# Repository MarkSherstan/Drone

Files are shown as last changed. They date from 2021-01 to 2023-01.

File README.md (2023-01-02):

# Drone
Mechanical, electrical, and software package for a custom quadcopter drone.

## Mechanical 
Designed using Fusion 360 and 3D printed on a Prusa MK3 printer. 

## Electrical
Custom PCBs designed in KiCad for the brain, power distribution, and signal indication. 
- Flight Controller
- Power Distribution Board 
- Lights 

## Software
C++ and custom libraries for controlling and stabilizing the UAV. Compiled with PlatformIO.

## Future Ideas
### Electrical
- Design ESCs
- 3.3 V flight controller (8 MHz suffcient?)
- Polyfuses on outputs
- PDB also ESC (active cooling?) - Have regulated outputs 
- PDB is part of frame (1 Oz copper)
- More powerful chip - RPi / STM32 / 2560 - Internet connection?

### Software 
- Test the crystal: How much time are we loosing? Try different caps.

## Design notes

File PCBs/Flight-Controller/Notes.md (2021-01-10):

## Crystal Capacitor Calcs
CL= (CX1 * CX2)/(CX1 + CX2) + CSTRAY
CL = (CX * CX)/(CX + CX) + CSTRAY <= substitute CX for CX1 and CX2 since they equal each other
CL = (CX^2)/(2CX) + CSTRAY
CL = (CX/2) + CSTRAY
CL - CSTRAY = (CX/2)
2*(CL -CSTRAY) = CX

CX1 = CX2 = 2*(CL-CSTRAY)

CSTRAY approx 4pF

22/2 = 11 - 4 = 7 ish 

https://blog.adafruit.com/2012/01/24/choosing-the-right-crystal-and-caps-for-your-design/
C1, C2 = 2*CL – 2*Cstray

https://forum.digikey.com/t/crystal-oscillator-load-cap-selection/1915
C1, C2 = 2*(CL) - Cstray

load capacitance of crystal * 2 - stray cap pin and trace = cap size 
https://www.microchip.com/forums/m881105.aspx
https://www.sparkfun.com/products/94

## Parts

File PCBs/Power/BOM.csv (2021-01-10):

Reference(s) | Qty | Value | LibPart | Footprint | Digi-Key # | Manufacturer | Manufacturer #
H1, H2, H3, H4 | 4 | M2 | Mechanical:MountingHole | MountingHole:MountingHole_2.2mm_M2_ISO14580_Pad
J1 | 1 | Power in SMD | Connector_Generic:Conn_01x02 | Custom:SMD-Power
J2 | 1 | Power in THR | Connector_Generic:Conn_01x02 | Custom:THR-Power
J3 | 1 | Corner 1 | Connector_Generic:Conn_01x02 | Custom:Corner-Pad
J4 | 1 | Corner 2 | Connector_Generic:Conn_01x02 | Custom:Corner-Pad
J5 | 1 | Corner 3 | Connector_Generic:Conn_01x02 | Custom:Corner-Pad
J6 | 1 | Corner 4 | Connector_Generic:Conn_01x02 | Custom:Corner-Pad
J7 | 1 | Flight Controller | Connector_Generic:Conn_01x06 | Connector_JST:JST_GH_BM06B-GHS-TBT_1x06-1MP_P1.25mm_Vertical | 455-1582-1-ND | JST Sales America Inc. | BM06B-GHS-TBT(LF)(SN)(N)
J8 | 1 | Flight Controller | Connector_Generic:Conn_01x06 | Connector_JST:JST_GH_SM06B-GHS-TB_1x06-1MP_P1.25mm_Horizontal | 455-1568-1-ND | JST Sales America Inc. | SM06B-GHS-TB(LF)(SN)

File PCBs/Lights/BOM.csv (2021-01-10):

Reference(s) | Qty | Value | LibPart | Footprint | Digi-Key # | Digi-Key Link Digi Link Digi-Key Link | Manufacturer | Manufacturer #
C1 | 1 | 1 uF 16V 10% | Device:C | Capacitor_SMD:C_0603_1608Metric_Pad1.05x0.95mm_HandSolder
D1 | 1 | See Notes | Device:LED | LED_SMD:LED_0603_1608Metric_Pad1.05x0.95mm_HandSolder
H1, H2 | 2 | M2 | Mechanical:MountingHole | MountingHole:MountingHole_2.2mm_M2_ISO14580_Pad
J1 | 1 | Conn_01x02 | Connector_Generic:Conn_01x02 | Connector_JST:JST_GH_SM02B-GHS-TB_1x02-1MP_P1.25mm_Horizontal | 455-1564-1-ND | https://www.digikey.ca/en/products/detail/jst-sales-america-inc/SM02B-GHS-TB-LF-SN/807786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 | JST Sales America Inc. | SM02B-GHS-TB(LF)(SN)
R1 | 1 | See Notes | Device:R | Resistor_SMD:R_0603_1608Metric_Pad1.05x0.95mm_HandSolder

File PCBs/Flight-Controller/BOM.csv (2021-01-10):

Reference(s) | Qty | Value | LibPart | Footprint | Digi-Key # | Manufacturer | Manufacturer # | Digi-Key Link
C1, C10, C11, C12, C18, C22 | 6 | 1uF 16V X7R 10% | Device:C | Capacitor_SMD:C_0603_1608Metric_Pad1.05x0.95mm_HandSolder
C2, C6, C9, C13, C14, C15, C21, C23 | 8 | 0.1uF 16V X7R 10% | Device:C | Capacitor_SMD:C_0603_1608Metric_Pad1.05x0.95mm_HandSolder
C3 | 1 | 10nF 16V X7R 10% | Device:C | Capacitor_SMD:C_0603_1608Metric_Pad1.05x0.95mm_HandSolder
C4 | 1 | 0.47uF 16V X7R 10% | Device:C | Capacitor_SMD:C_0603_1608Metric_Pad1.05x0.95mm_HandSolder
C5 | 1 | 2.2uF 16V X7R 10% | Device:C | Capacitor_SMD:C_0603_1608Metric_Pad1.05x0.95mm_HandSolder
C7, C8 | 2 | 22pF 12V X7R 2% | Device:C | Capacitor_SMD:C_0603_1608Metric_Pad1.05x0.95mm_HandSolder
C16 | 1 | 0.1uF 20V X7R 10% | Device:C | Capacitor_SMD:C_0603_1608Metric_Pad1.05x0.95mm_HandSolder
C17 | 1 | 10uF 20V 20% | Device:CP | Capacitor_SMD:C_0603_1608Metric_Pad1.05x0.95mm_HandSolder
C19, C20 | 2 | 22uF 16V 20% | Device:CP | Capacitor_SMD:C_0603_1608Metric_Pad1.05x0.95mm_HandSolder
D1 | 1 | LED_RGB | Custom:LED_RGB | Custom:RGB_LED | 1080-EAST1616RGBA4CT-ND | Everlight Electronics Co Ltd | EAST1616RGBA4 | https://www.digikey.ca/en/products/detail/everlight-electronics-co-ltd/EAST1616RGBA4/11200796
D2, D3 | 2 | Green 2.2V 20mA | Device:LED | LED_SMD:LED_0603_1608Metric_Pad1.05x0.95mm_HandSolder
D4 | 1 | 75V 150mA | Device:D | Diode_SMD:D_0603_1608Metric_Pad1.05x0.95mm_HandSolder | TS4148CRZGCT-ND | Taiwan Semiconductor Corporation | TS4148C RZG | https://www.digikey.ca/en/products/detail/taiwan-semiconductor-corporation/TS4148C-RZG/7359811
D5, D6 | 2 | Orange 2V 20mA | Device:LED | LED_SMD:LED_0603_1608Metric_Pad1.05x0.95mm_HandSolder
F1 | 1 | PTC 15V 500mA | Device:Polyfuse_Small | Fuse:Fuse_1206_3216Metric_Pad1.42x1.75mm_HandSolder | 283-3140-1-ND | Eaton - Electronics Division | PTS120615V050 | https://www.digikey.ca/en/products/detail/eaton-electronics-division/PTS120615V050/2639137
FB1 | 1 | Ferrite 30 ohm 1 line | Device:Ferrite_Bead | Resistor_SMD:R_0603_1608Metric_Pad1.05x0.95mm_HandSolder | MH1608-300YCT-ND | Bourns Inc. | MH1608-300Y | https://www.digikey.ca/en/products/detail/bourns-inc/MH1608-300Y/1970497
H1, H2, H3, H4 | 4 | M2 | Mechanical:MountingHole | MountingHole:MountingHole_2.2mm_M2_ISO7380_Pad
J1 | 1 | ESC_1 | Connector_Generic:Conn_01x05 | Connector_JST:JST_GH_BM05B-GHS-TBT_1x05-1MP_P1.25mm_Vertical | 455-1581-1-ND | JST Sales America Inc. | BM05B-GHS-TBT(LF)(SN)(N) | https://www.digikey.ca/en/products/detail/jst-sales-america-inc/BM05B-GHS-TBT-LF-SN-N/807803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
J2 | 1 | Receiver | Connector_Generic:Conn_01x07 | Connector_JST:JST_GH_BM07B-GHS-TBT_1x07-1MP_P1.25mm_Vertical | 455-1583-1-ND | JST Sales America Inc. | BM07B-GHS-TBT(LF)(SN)(N) | https://www.digikey.ca/en/products/detail/jst-sales-america-inc/BM07B-GHS-TBT-LF-SN-N/807805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
J3 | 1 | ESC_2 | Connector_Generic:Conn_01x05 | Connector_JST:JST_GH_BM05B-GHS-TBT_1x05-1MP_P1.25mm_Vertical | 455-1581-1-ND | JST Sales America Inc. | BM05B-GHS-TBT(LF)(SN)(N) | https://www.digikey.ca/en/products/detail/jst-sales-america-inc/BM05B-GHS-TBT-LF-SN-N/807803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
J4 | 1 | ICSP | Connector_Generic:Conn_02x03_Odd_Even | Connector_PinHeader_2.54mm:PinHeader_2x03_P2.54mm_Vertical
J5 | 1 | ESC_3 | Connector_Generic:Conn_01x05 | Connector_JST:JST_GH_BM05B-GHS-TBT_1x05-1MP_P1.25mm_Vertical | 455-1581-1-ND | JST Sales America Inc. | BM05B-GHS-TBT(LF)(SN)(N) | https://www.digikey.ca/en/products/detail/jst-sales-america-inc/BM05B-GHS-TBT-LF-SN-N/807803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
J6 | 1 | Aux | Connector_Generic:Conn_01x04 | Connector_JST:JST_GH_BM04B-GHS-TBT_1x04-1MP_P1.25mm_Vertical | 455-1580-1-ND | JST Sales America Inc. | BM04B-GHS-TBT(LF)(SN)(N) | https://www.digikey.ca/en/products/detail/jst-sales-america-inc/BM04B-GHS-TBT-LF-SN-N/807802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
J7 | 1 | ESC_4 | Connector_Generic:Conn_01x05 | Connector_JST:JST_GH_BM05B-GHS-TBT_1x05-1MP_P1.25mm_Vertical | 455-1581-1-ND | JST Sales America Inc. | BM05B-GHS-TBT(LF)(SN)(N) | https://www.digikey.ca/en/products/detail/jst-sales-america-inc/BM05B-GHS-TBT-LF-SN-N/807803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
J8 | 1 | Power_In | Connector_Generic:Conn_01x06 | Connector_JST:JST_GH_BM06B-GHS-TBT_1x06-1MP_P1.25mm_Vertical | 455-1582-1-ND | JST Sales America Inc. | BM06B-GHS-TBT(LF)(SN)(N) | https://www.digikey.ca/en/products/detail/jst-sales-america-inc/BM06B-GHS-TBT-LF-SN-N/807804
J9 | 1 | USB_B_Micro | Connector:USB_B_Micro | Connector_USB:USB_Micro-B_Molex-105017-0001 | WM1399CT-ND | Molex | 105017-0001 | https://www.digikey.ca/en/products/detail/molex/1050170001/2350832
Q1, Q2 | 2 | BSS138 | Transistor_FET:BSS138 | Package_TO_SOT_SMD:SOT-23 | BSS138CT-ND | ON Semiconductor | BSS138 | https://www.digikey.ca/en/products/detail/on-semiconductor/BSS138/244210
Q3, Q4 | 2 | PMV48XP,215 | Device:Q_PMOS_GSD | Package_TO_SOT_SMD:SOT-23 | 1727-5907-1-ND | Nexperia USA Inc. | PMV48XP,215 | https://www.digikey.ca/en/products/detail/nexperia-usa-inc/PMV48XP215/2744664
R1 | 1 | 3.2 kohm 1% | Device:R | Resistor_SMD:R_0603_1608Metric_Pad1.05x0.95mm_HandSolder
R2 | 1 | 2 kohm 1% | Device:R | Resistor_SMD:R_0603_1608Metric_Pad1.05x0.95mm_HandSolder
R3, R5 | 2 | 100 ohm 5% | Device:R | Resistor_SMD:R_0603_1608Metric_Pad1.05x0.95mm_HandSolder
R4, R6 | 2 | 150 ohm 5% | Device:R | Resistor_SMD:R_0603_1608Metric_Pad1.05x0.95mm_HandSolder
R7 | 1 | 55 ohm 5% | Device:R | Resistor_SMD:R_0603_1608Metric_Pad1.05x0.95mm_HandSolder
R8, R9, R10, R11, R12, R13, R14, R17, R18, R19 | 10 | 10 kohm 5% | Device:R | Resistor_SMD:R_0603_1608Metric_Pad1.05x0.95mm_HandSolder
R15, R16 | 2 | 1 kohm 5% | Device:R | Resistor_SMD:R_0603_1608Metric_Pad1.05x0.95mm_HandSolder
R20, R21 | 2 | 22 ohm 1% | Device:R | Resistor_SMD:R_0603_1608Metric_Pad1.05x0.95mm_HandSolder
RV1, RV2 | 2 | 5V 0.5pF | Device:Varistor | Resistor_SMD:R_0603_1608Metric_Pad1.05x0.95mm_HandSolder | CG0603MLC-05ECT-ND | Bourns Inc. | CG0603MLC-05E | https://www.digikey.ca/en/products/detail/bourns-inc/CG0603MLC-05E/2538084
SW1 | 1 | Push-Switch | Custom:Push-Switch | Custom:Switch | CKN10361CT-ND | C&K | RS-187R05A2-DS MT RT | https://www.digikey.ca/en/products/detail/c-k/RS-187R05A2-DS-MT-RT/2747186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
U1 | 1 | MCP6001U | Amplifier_Operational:MCP6001U | Package_TO_SOT_SMD:SOT-23-5 | MCP6001UT-I/OTCT-ND | Microchip Technology | MCP6001UT-I/OT | https://www.digikey.ca/en/products/detail/microchip-technology/MCP6001UT-I-OT/562450
U2 | 1 | ICM-20689 | Custom:ICM-20689 | Package_DFN_QFN:QFN-24-1EP_4x4mm_P0.5mm_EP2.8x2.8mm | 1428-1059-1-ND | TDK InvenSense | ICM-20689 | https://www.digikey.ca/en/products/detail/tdk-invensense/ICM-20689/5872869
U3 | 1 | ATmega32U4-AU | Flight-Controller-PCB-rescue:ATmega32U4-AU-MCU_Microchip_ATmega-Flight-Controller-PCB-rescue | Package_QFP:TQFP-44_10x10mm_P0.8mm | ATMEGA32U4RC-AU-ND | Microchip Technology | ATMEGA32U4RC-AU | https://www.digikey.ca/en/products/detail/microchip-technology/ATMEGA32U4RC-AU/2507982
U4 | 1 | LM1117-5.0 | Custom:LM1117-5.0 | Package_TO_SOT_SMD:SOT-223 | LM1117IMP-5.0/NOPBCT-ND | Texas Instruments | LM1117IMP-5.0/NOPB | https://www.digikey.ca/en/products/detail/texas-instruments/LM1117IMP-5-0-NOPB/482940
U5 | 1 | LP2985-3.3 | Regulator_Linear:LP2985-3.3 | Package_TO_SOT_SMD:SOT-23-5 | 296-18476-1-ND | Texas Instruments | LP2985-33DBVR | https://www.digikey.ca/en/products/detail/texas-instruments/LP2985-33DBVR/809759
Y1 | 1 | 16MHz, CL 7pF | Device:Crystal | Custom:Crystal | 535-14027-1-ND | Abracon LLC | ABM8W-16.0000MHZ-7-D1X-T3 | https://www.digikey.ca/en/products/detail/abracon-llc/ABM8W-16-0000MHZ-7-D1X-T3/7172798

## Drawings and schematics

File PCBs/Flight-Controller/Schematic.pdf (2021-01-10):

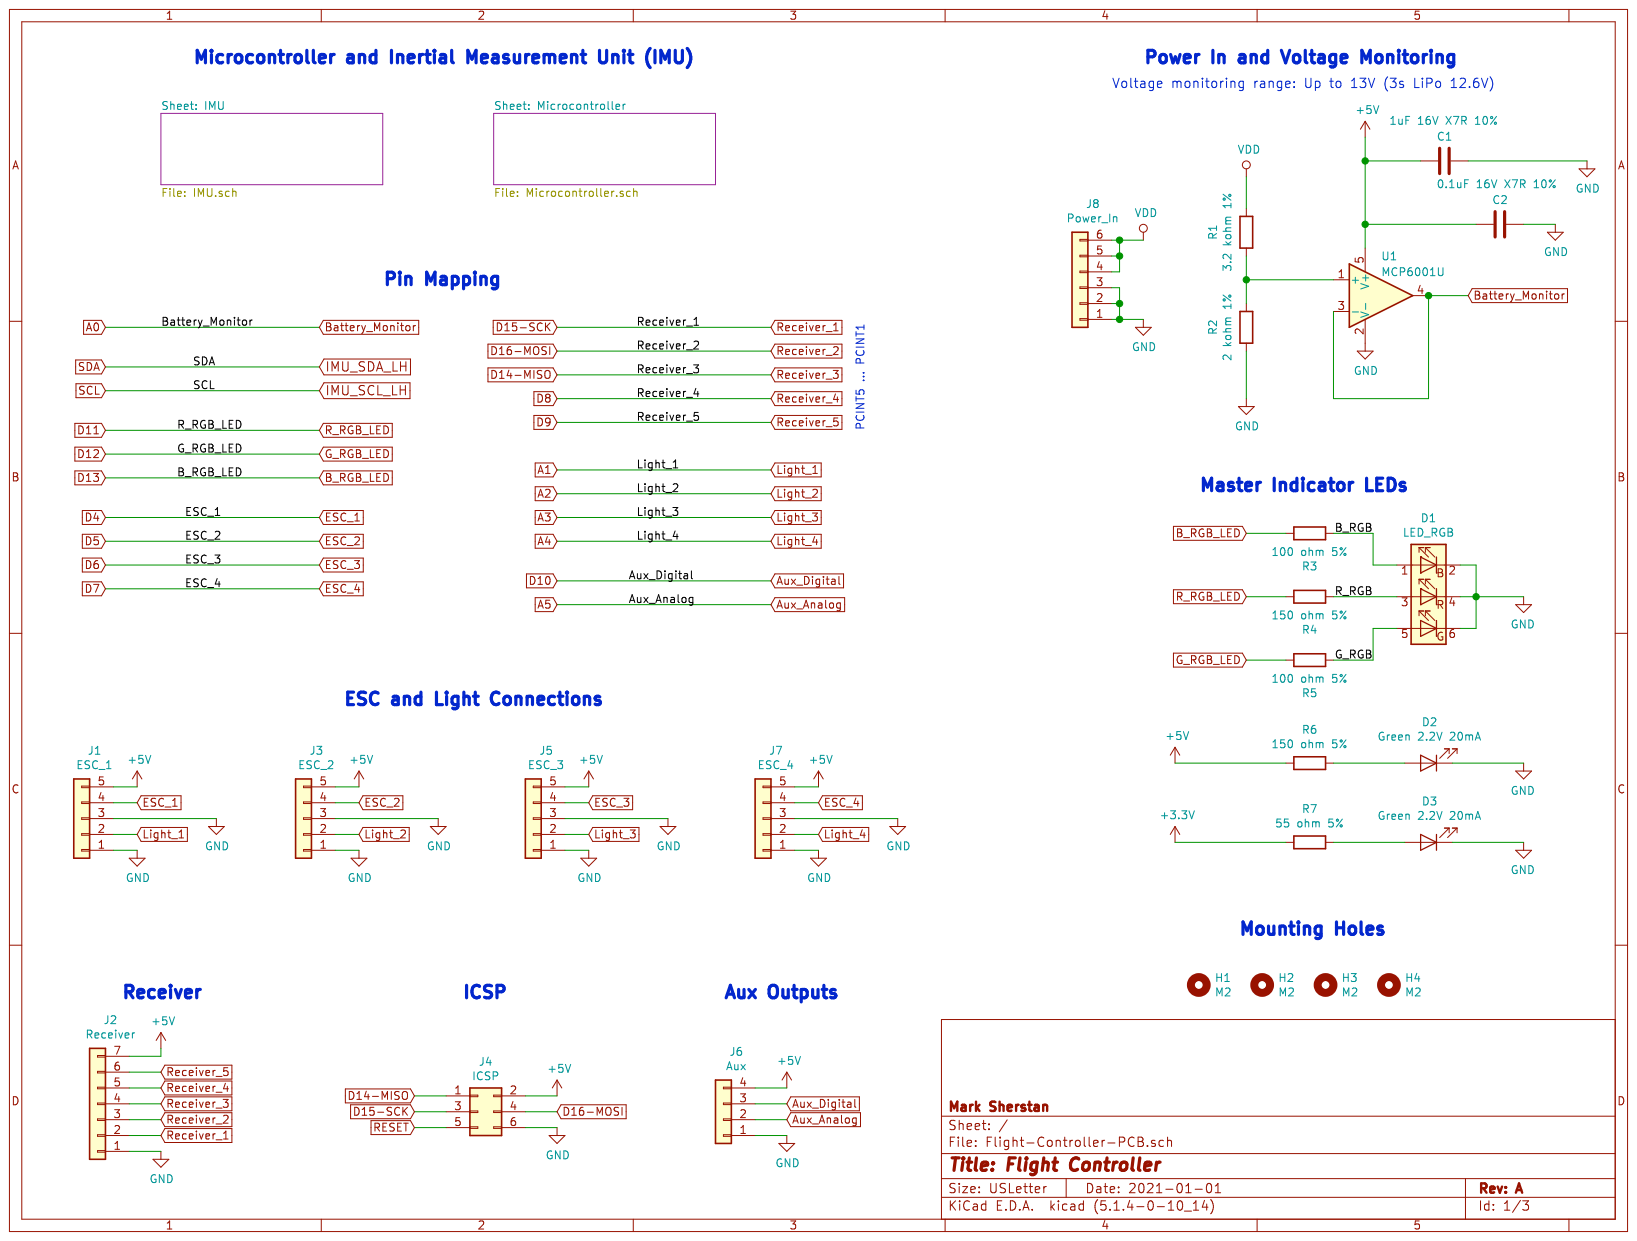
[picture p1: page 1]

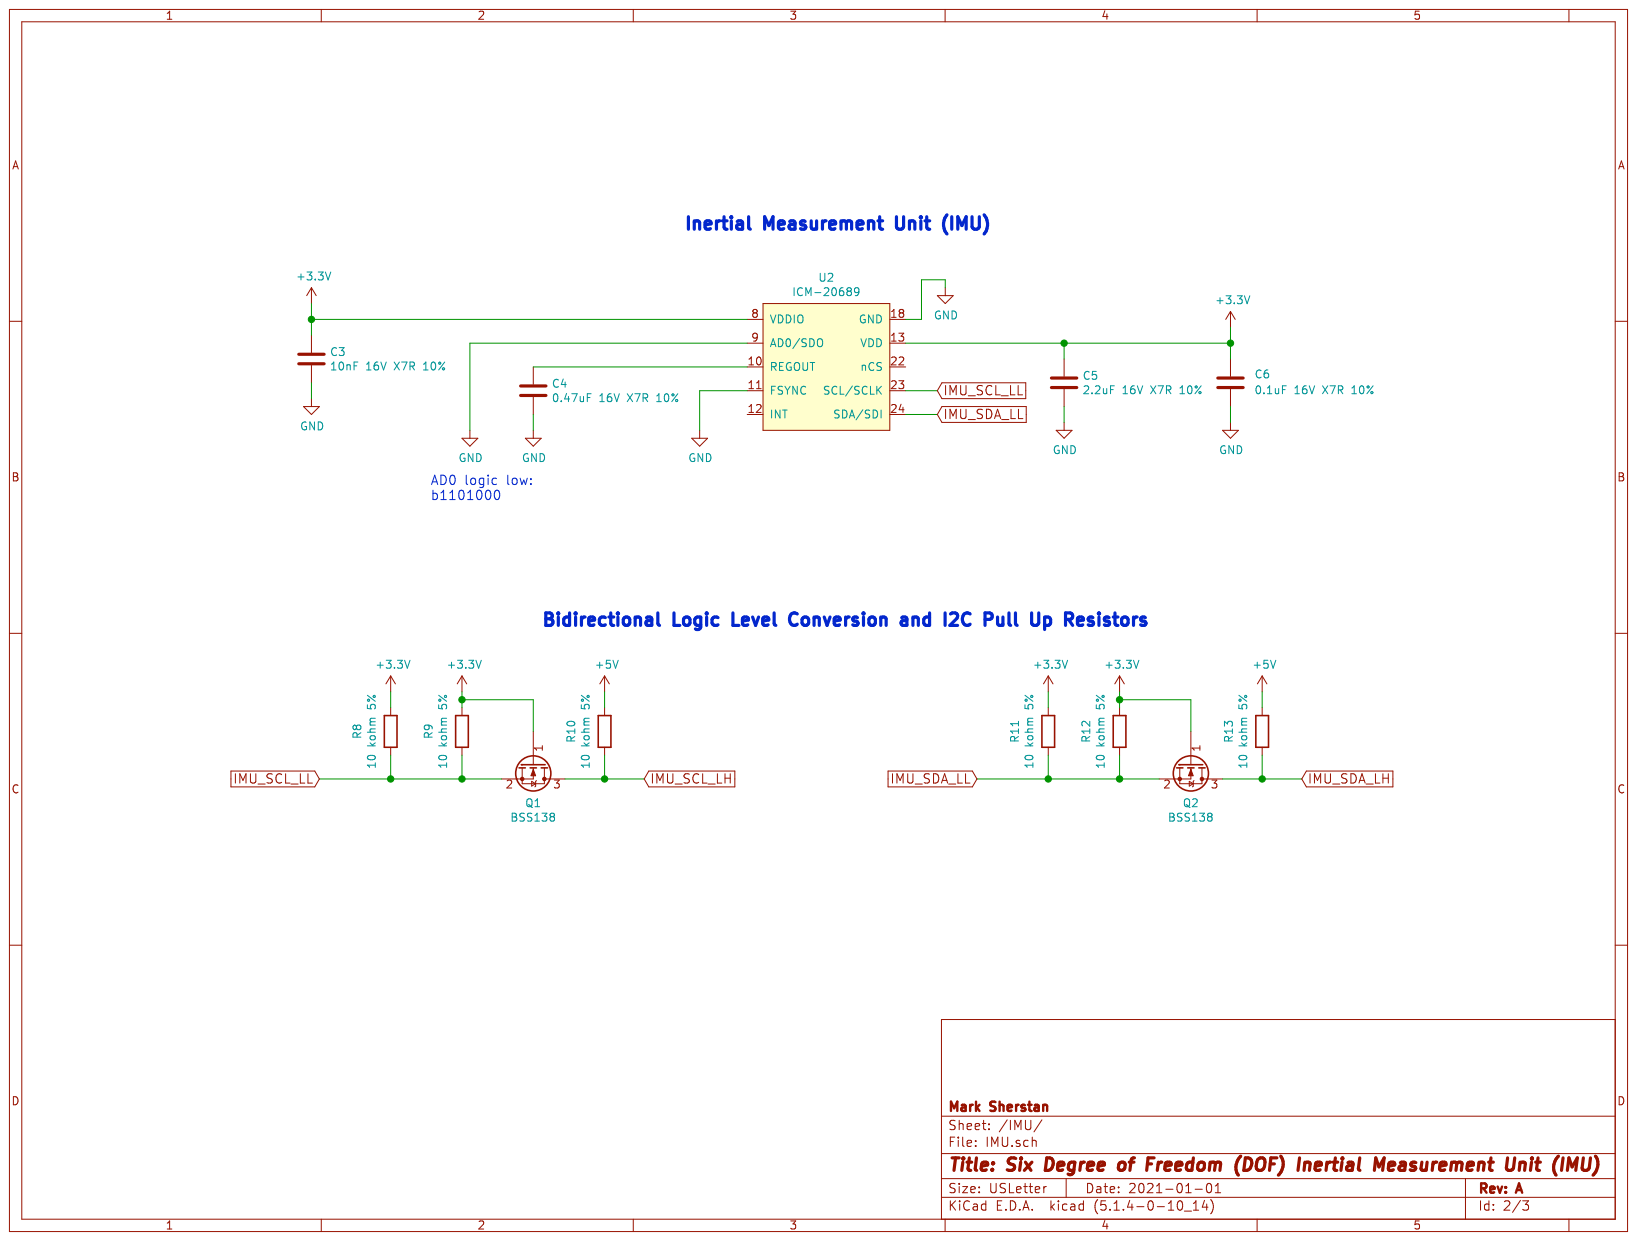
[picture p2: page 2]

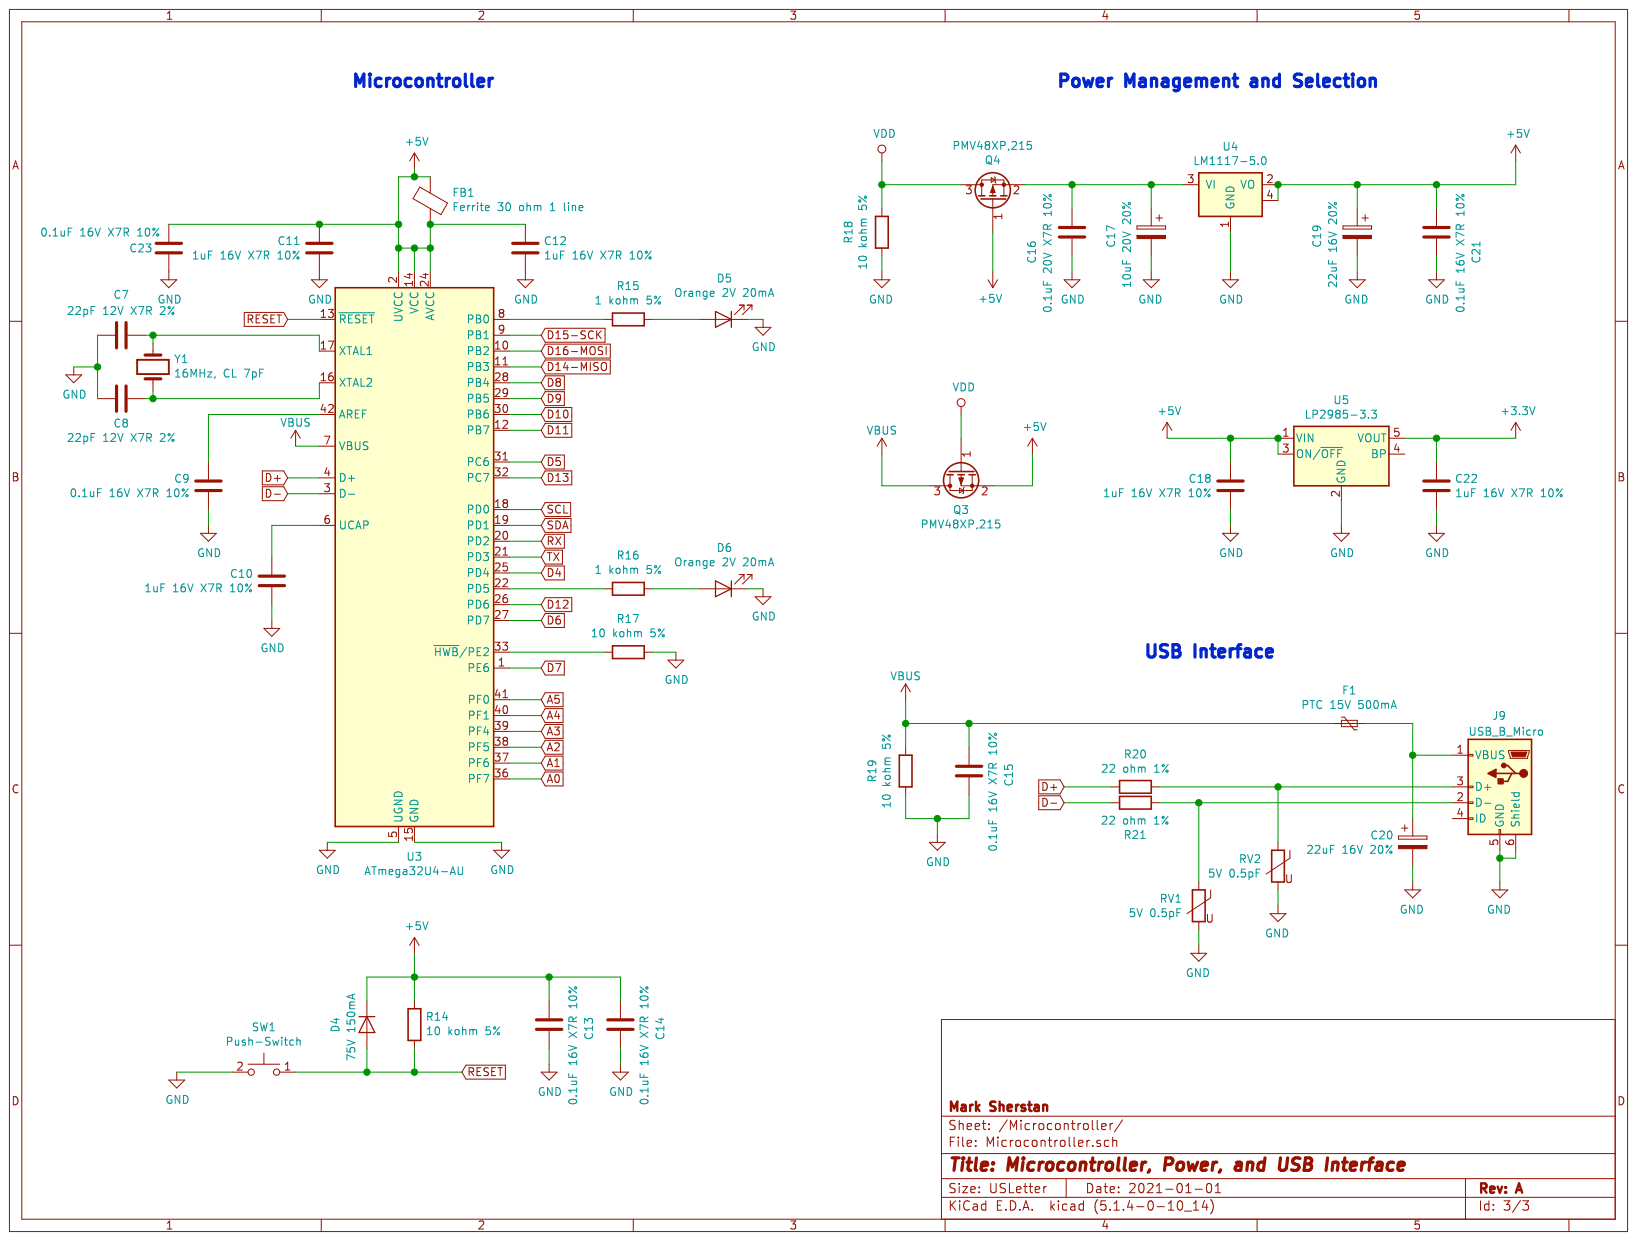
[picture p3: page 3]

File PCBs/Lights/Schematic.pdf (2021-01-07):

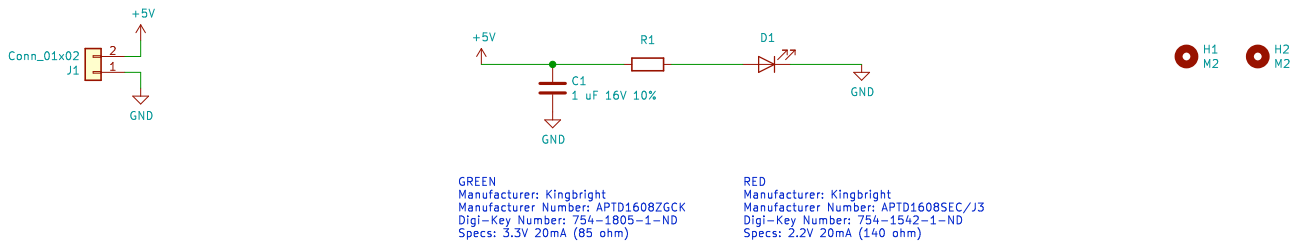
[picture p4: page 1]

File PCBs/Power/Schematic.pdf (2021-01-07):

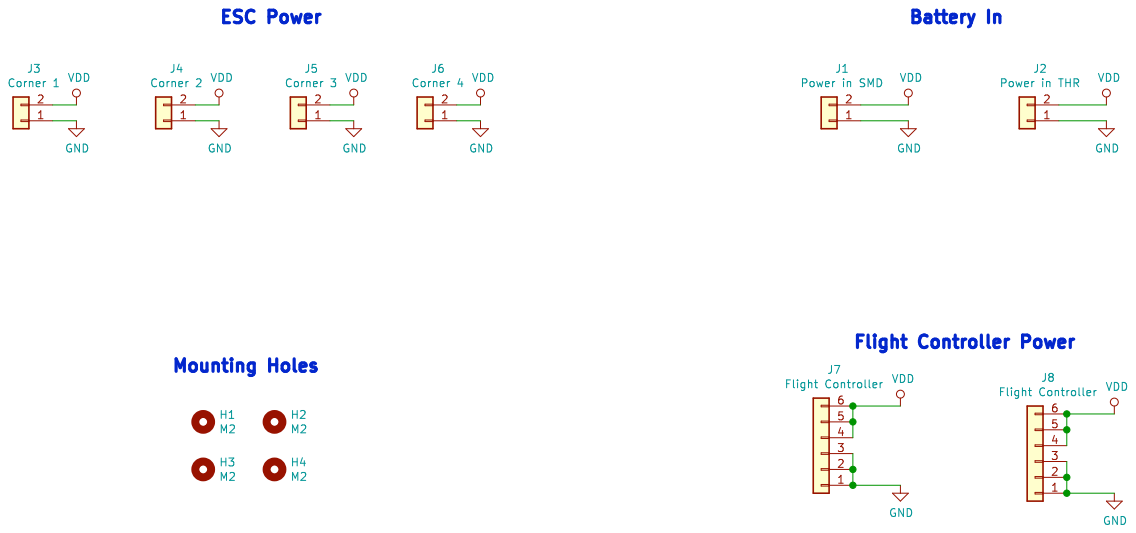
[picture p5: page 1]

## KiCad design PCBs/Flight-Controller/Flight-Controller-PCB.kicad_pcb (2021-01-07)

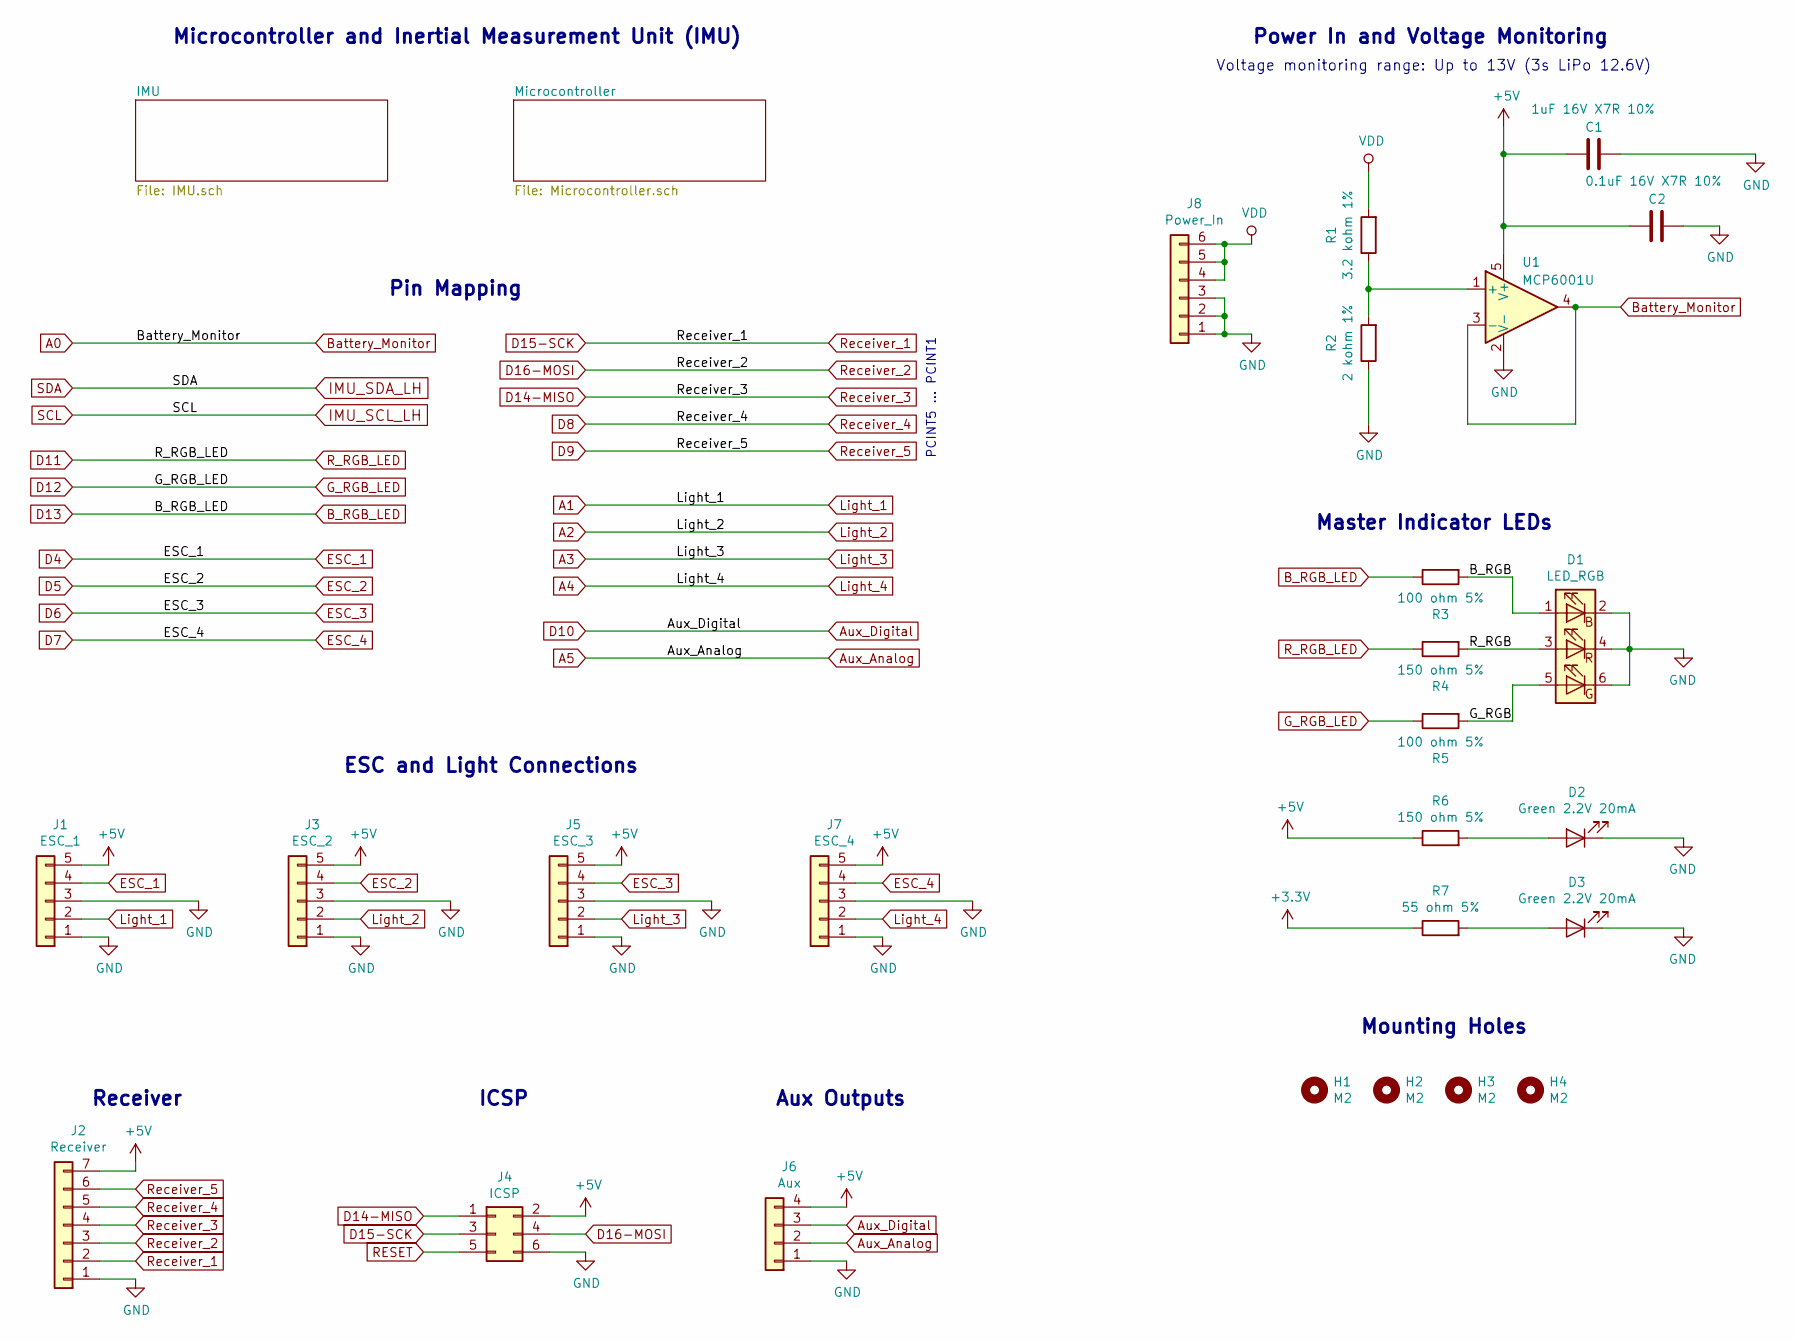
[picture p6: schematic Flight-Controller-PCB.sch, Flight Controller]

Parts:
C1: 1uF 16V X7R 10%; C_0603_1608Metric_Pad1.05x0.95mm_HandSolder
C2: 0.1uF 16V X7R 10%; C_0603_1608Metric_Pad1.05x0.95mm_HandSolder
D1: LED_RGB; RGB_LED; Manufacturer # EAST1616RGBA4; Digi-Key # 1080-EAST1616RGBA4CT-ND
D2, D3: Green 2.2V 20mA; LED_0603_1608Metric_Pad1.05x0.95mm_HandSolder
H1, H2, H3, H4: M2; MountingHole_2.2mm_M2_ISO7380_Pad
J1: ESC_1; JST_GH_BM05B-GHS-TBT_1x05-1MP_P1.25mm_Vertical; Manufacturer # BM05B-GHS-TBT(LF)(SN)(N); Digi-Key # 455-1581-1-ND
J2: Receiver; JST_GH_BM07B-GHS-TBT_1x07-1MP_P1.25mm_Vertical; Manufacturer # BM07B-GHS-TBT(LF)(SN)(N); Digi-Key # 455-1583-1-ND
J3: ESC_2; JST_GH_BM05B-GHS-TBT_1x05-1MP_P1.25mm_Vertical; Manufacturer # BM05B-GHS-TBT(LF)(SN)(N); Digi-Key # 455-1581-1-ND
J4: ICSP; PinHeader_2x03_P2.54mm_Vertical
J5: ESC_3; JST_GH_BM05B-GHS-TBT_1x05-1MP_P1.25mm_Vertical; Manufacturer # BM05B-GHS-TBT(LF)(SN)(N); Digi-Key # 455-1581-1-ND
J6: Aux; JST_GH_BM04B-GHS-TBT_1x04-1MP_P1.25mm_Vertical; Manufacturer # BM04B-GHS-TBT(LF)(SN)(N); Digi-Key # 455-1580-1-ND
J7: ESC_4; JST_GH_BM05B-GHS-TBT_1x05-1MP_P1.25mm_Vertical; Manufacturer # BM05B-GHS-TBT(LF)(SN)(N); Digi-Key # 455-1581-1-ND
J8: Power_In; JST_GH_BM06B-GHS-TBT_1x06-1MP_P1.25mm_Vertical; Manufacturer # BM06B-GHS-TBT(LF)(SN)(N); Digi-Key # 455-1582-1-ND
R1: 3.2 kohm 1%; R_0603_1608Metric_Pad1.05x0.95mm_HandSolder
R2: 2 kohm 1%; R_0603_1608Metric_Pad1.05x0.95mm_HandSolder
R3, R5: 100 ohm 5%; R_0603_1608Metric_Pad1.05x0.95mm_HandSolder
R4, R6: 150 ohm 5%; R_0603_1608Metric_Pad1.05x0.95mm_HandSolder
R7: 55 ohm 5%; R_0603_1608Metric_Pad1.05x0.95mm_HandSolder
U1: MCP6001U; SOT-23-5; Manufacturer # MCP6001UT-I/OT; Digi-Key # MCP6001UT-I/OTCT-ND

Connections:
+3V3: R7.1; also elsewhere on the board
+5V: C1.2, C2.2, J1.5, J2.7, J3.5, J4.2, J5.5, J6.4, J7.5, R6.1, U1.5 (V+); also elsewhere on the board
/B_RGB: D1.1 (RA), R3.2
/G_RGB: D1.5 (BA), R5.2
/R_RGB: D1.3 (GA), R4.2
A0: U1.3 (-), U1.4; also elsewhere on the board
A1: J1.2; also elsewhere on the board
A2: J3.2; also elsewhere on the board
A3: J5.2; also elsewhere on the board
A4: J7.2; also elsewhere on the board
A5: J6.2; also elsewhere on the board
Aux_Digital: J6.3; also elsewhere on the board
B_RGB_LED: R3.1; also elsewhere on the board
D4: J1.4; also elsewhere on the board
D5: J3.4; also elsewhere on the board
D6: J5.4; also elsewhere on the board
D7: J7.4; also elsewhere on the board
D8: J2.5; also elsewhere on the board
D9: J2.6; also elsewhere on the board
D11: R4.1; also elsewhere on the board
D12: R5.1; also elsewhere on the board
D14-MISO: J2.4, J4.1; also elsewhere on the board
D15-SCK: J2.2, J4.3; also elsewhere on the board
D16-MOSI: J2.3, J4.4; also elsewhere on the board
GND: C1.1, C2.1, D1.2 (RK), D1.4 (GK), D1.6 (BK), D2.1 (K), D3.1 (K), J1.1, J1.3, J2.1, J3.1, J3.3, J4.6, J5.1, J5.3, J6.1, J7.1, J7.3, J8.1, J8.2, J8.3, R2.1, U1.2 (V-); also elsewhere on the board
unnamed: D2.2 (A), R6.2
unnamed: D3.2 (A), R7.2
unnamed: R1.1, R2.2, U1.1 (+)
RESET: J4.5; also elsewhere on the board
VDD: J8.4, J8.5, J8.6, R1.2; also elsewhere on the board

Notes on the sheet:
Power In and Voltage Monitoring
Microcontroller and Inertial Measurement Unit (IMU)
Pin Mapping
ESC and Light Connections
Mounting Holes
Voltage monitoring range: Up to 13V (3s LiPo 12.6V)
Receiver
Aux Outputs
Master Indicator LEDs
ICSP
PCINT5 … PCINT1

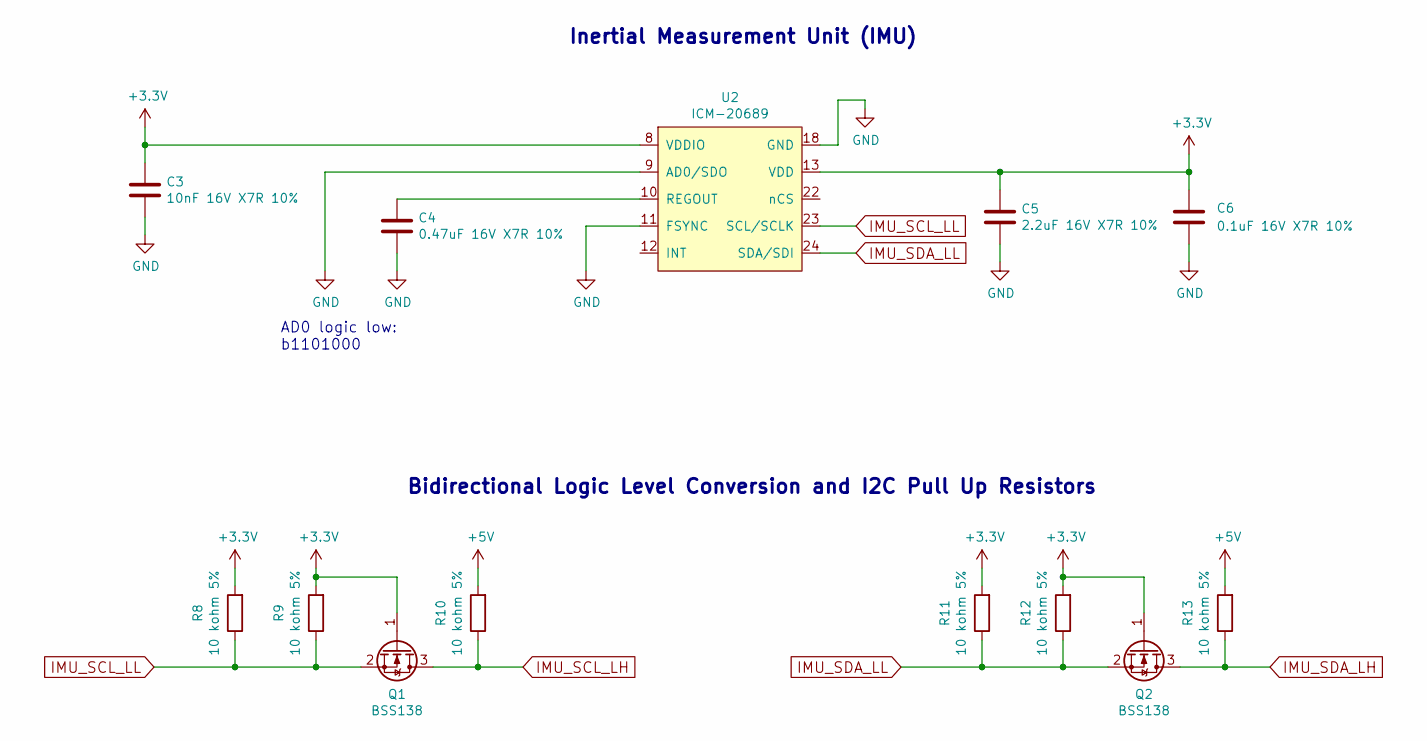
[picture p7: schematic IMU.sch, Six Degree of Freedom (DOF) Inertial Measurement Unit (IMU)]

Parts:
C3: 10nF 16V X7R 10%; C_0603_1608Metric_Pad1.05x0.95mm_HandSolder
C4: 0.47uF 16V X7R 10%; C_0603_1608Metric_Pad1.05x0.95mm_HandSolder
C5: 2.2uF 16V X7R 10%; C_0603_1608Metric_Pad1.05x0.95mm_HandSolder
C6: 0.1uF 16V X7R 10%; C_0603_1608Metric_Pad1.05x0.95mm_HandSolder
Q1, Q2: BSS138; SOT-23; Manufacturer # BSS138; Digi-Key # BSS138CT-ND
R8, R9, R10, R11, R12, R13: 10 kohm 5%; R_0603_1608Metric_Pad1.05x0.95mm_HandSolder
U2: ICM-20689; QFN-24-1EP_4x4mm_P0.5mm_EP2.8x2.8mm; Manufacturer # ICM-20689; Digi-Key # 1428-1059-1-ND

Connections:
+3V3: C3.1, C5.1, C6.2, Q1.1 (G), Q2.1 (G), R8.2, R9.2, R11.2, R12.2, U2.8 (VDDIO), U2.13 (VDD); also elsewhere on the board
+5V: R10.2, R13.2; also elsewhere on the board
GND: C3.2, C4.2, C5.2, C6.1, U2.9 (AD0/SDO), U2.11 (FSYNC), U2.18 (GND); also elsewhere on the board
IMU_SCL_LL: Q1.2 (S), R8.1, R9.1, U2.23 (SCL/SCLK)
IMU_SDA_LL: Q2.2 (S), R11.1, R12.1, U2.24 (SDA/SDI)
unnamed: C4.1, U2.10 (REGOUT)

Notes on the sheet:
AD0 logic low: b1101000
Inertial Measurement Unit (IMU)
Bidirectional Logic Level Conversion and I2C Pull Up Resistors

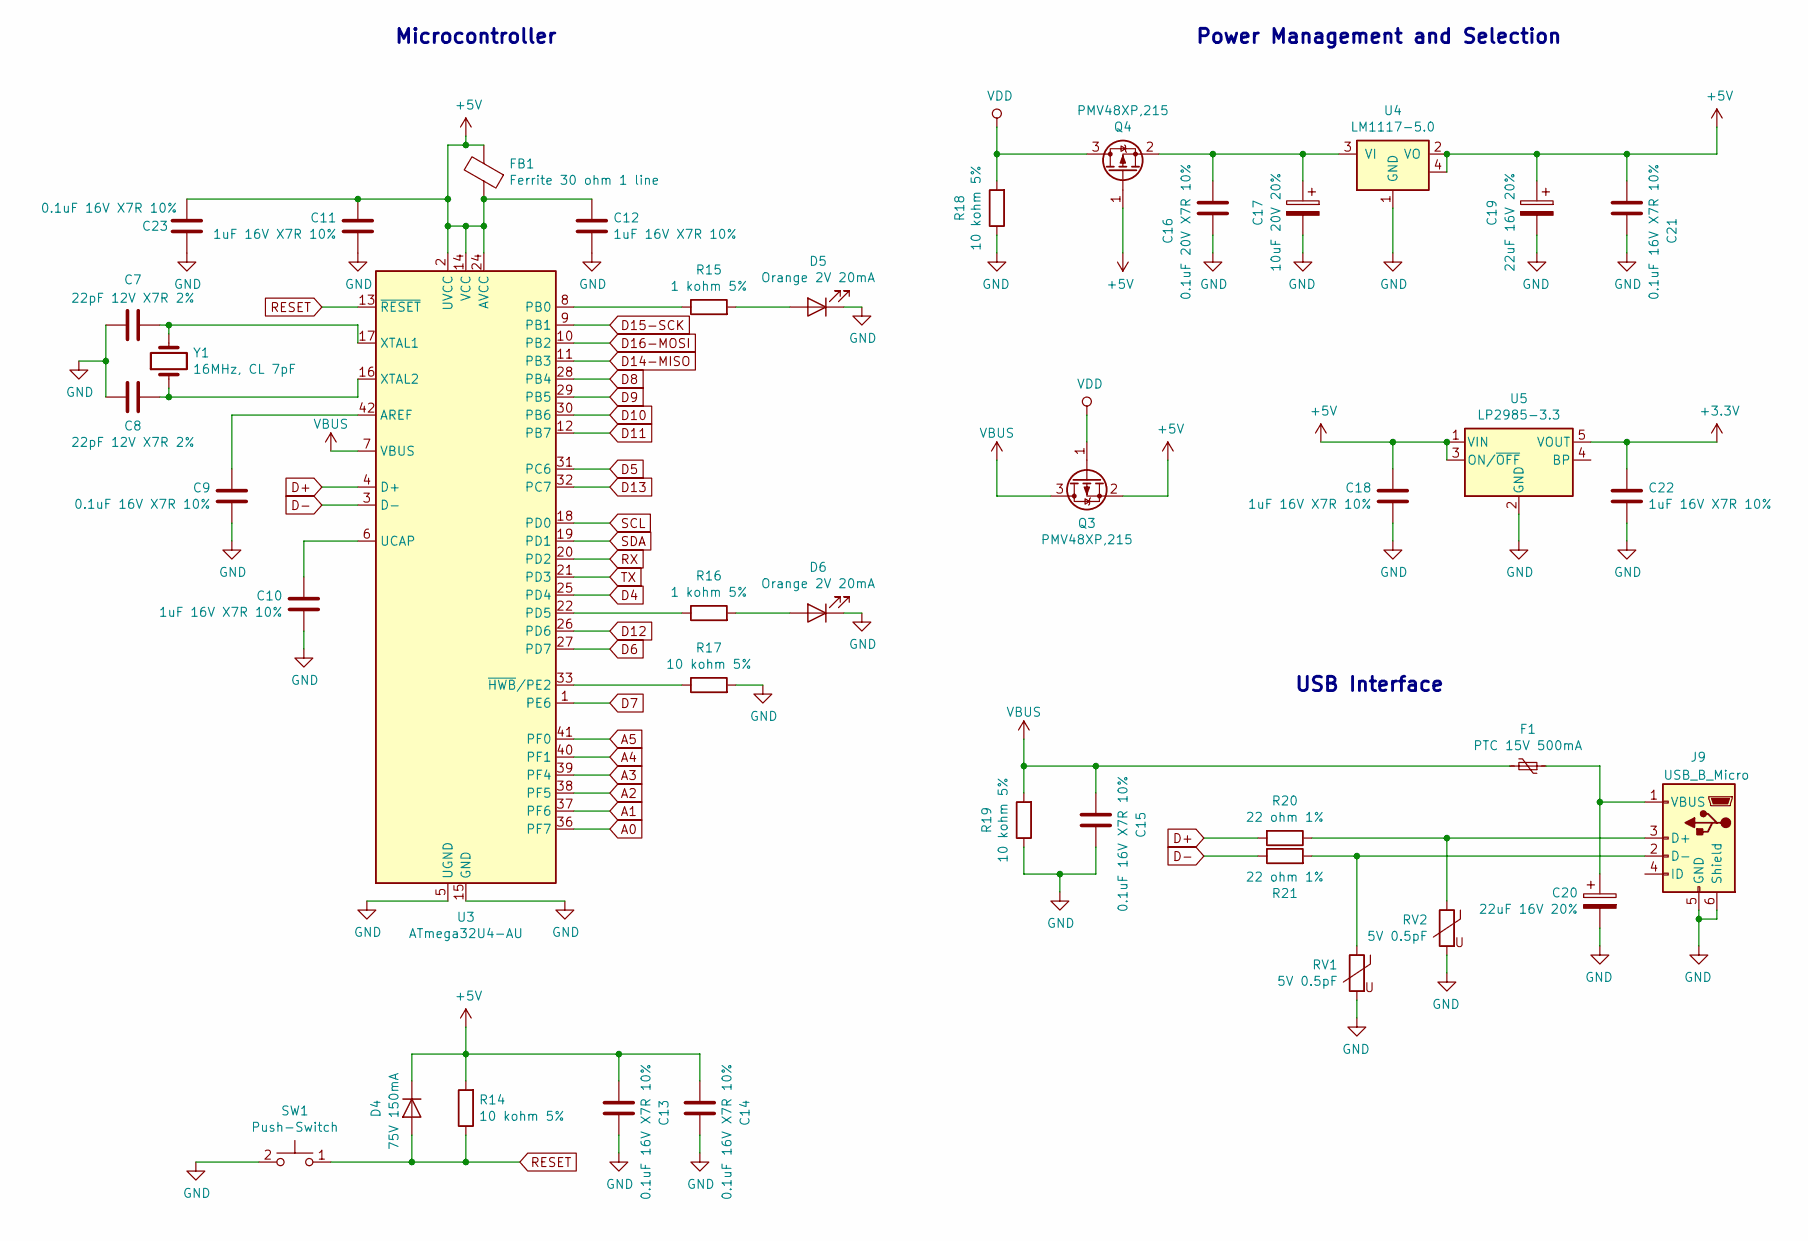
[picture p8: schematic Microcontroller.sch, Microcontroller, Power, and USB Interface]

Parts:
C7, C8: 22pF 12V X7R 2%; C_0603_1608Metric_Pad1.05x0.95mm_HandSolder
C9, C13, C14, C15, C21, C23: 0.1uF 16V X7R 10%; C_0603_1608Metric_Pad1.05x0.95mm_HandSolder
C10, C11, C12, C18, C22: 1uF 16V X7R 10%; C_0603_1608Metric_Pad1.05x0.95mm_HandSolder
C16: 0.1uF 20V X7R 10%; C_0603_1608Metric_Pad1.05x0.95mm_HandSolder
C17: 10uF 20V 20%; C_0603_1608Metric_Pad1.05x0.95mm_HandSolder
C19, C20: 22uF 16V 20%; C_0603_1608Metric_Pad1.05x0.95mm_HandSolder
D4: 75V 150mA; D_0603_1608Metric_Pad1.05x0.95mm_HandSolder; Manufacturer # TS4148C RZG; Digi-Key # TS4148CRZGCT-ND
D5, D6: Orange 2V 20mA; LED_0603_1608Metric_Pad1.05x0.95mm_HandSolder
F1: PTC 15V 500mA; Fuse_1206_3216Metric_Pad1.42x1.75mm_HandSolder; Manufacturer # PTS120615V050; Digi-Key # 283-3140-1-ND
FB1: Ferrite 30 ohm 1 line; R_0603_1608Metric_Pad1.05x0.95mm_HandSolder; Manufacturer # MH1608-300Y; Digi-Key # MH1608-300YCT-ND
J9: USB_B_Micro; USB_Micro-B_Molex-105017-0001; Manufacturer # 105017-0001; Digi-Key # WM1399CT-ND
Q3, Q4: PMV48XP,215; SOT-23; Manufacturer # PMV48XP,215; Digi-Key # 1727-5907-1-ND
R14, R17, R18, R19: 10 kohm 5%; R_0603_1608Metric_Pad1.05x0.95mm_HandSolder
R15, R16: 1 kohm 5%; R_0603_1608Metric_Pad1.05x0.95mm_HandSolder
R20, R21: 22 ohm 1%; R_0603_1608Metric_Pad1.05x0.95mm_HandSolder
RV1, RV2: 5V 0.5pF; R_0603_1608Metric_Pad1.05x0.95mm_HandSolder; Manufacturer # CG0603MLC-05E; Digi-Key # CG0603MLC-05ECT-ND
SW1: Push-Switch; Switch; Manufacturer # RS-187R05A2-DS MT RT; Digi-Key # CKN10361CT-ND
U3: ATmega32U4-AU; TQFP-44_10x10mm_P0.8mm; Manufacturer # ATMEGA32U4RC-AU; Digi-Key # ATMEGA32U4RC-AU-ND
U4: LM1117-5.0; SOT-223; Manufacturer # LM1117IMP-5.0/NOPB; Digi-Key # LM1117IMP-5.0/NOPBCT-ND
U5: LP2985-3.3; SOT-23-5; Manufacturer # LP2985-33DBVR; Digi-Key # 296-18476-1-ND
Y1: 16MHz, CL 7pF; Crystal; Manufacturer # ABM8W-16.0000MHZ-7-D1X-T3; Digi-Key # 535-14027-1-ND

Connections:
+3V3: C22.1, U5.5 (VOUT); also elsewhere on the board
+5V: C11.1, C12.1, C13.1, C14.1, C18.1, C19.1, C21.1, C23.1, D4.1 (K), FB1.1, FB1.2, Q3.2 (S), Q4.1 (G), R14.2, U3.2 (UVCC), U3.14 (VCC), U3.24 (AVCC), U3.34 (VCC), U3.44 (AVCC), U4.2 (VO), U4.4, U5.1 (VIN), U5.3 (ON/~OFF~); also elsewhere on the board
A0: U3.36 (PF7); also elsewhere on the board
A1: U3.37 (PF6); also elsewhere on the board
A2: U3.38 (PF5); also elsewhere on the board
A3: U3.39 (PF4); also elsewhere on the board
A4: U3.40 (PF1); also elsewhere on the board
A5: U3.41 (PF0); also elsewhere on the board
Aux_Digital: U3.30 (PB6); also elsewhere on the board
B_RGB_LED: U3.32 (PC7); also elsewhere on the board
D4: U3.25 (PD4); also elsewhere on the board
D5: U3.31 (PC6); also elsewhere on the board
D6: U3.27 (PD7); also elsewhere on the board
D7: U3.1 (PE6); also elsewhere on the board
D8: U3.28 (PB4); also elsewhere on the board
D9: U3.29 (PB5); also elsewhere on the board
D11: U3.12 (PB7); also elsewhere on the board
D12: U3.26 (PD6); also elsewhere on the board
D14-MISO: U3.11 (PB3); also elsewhere on the board
D15-SCK: U3.9 (PB1); also elsewhere on the board
D16-MOSI: U3.10 (PB2); also elsewhere on the board
D+: R20.2, U3.4 (D+)
D-: R21.1, U3.3 (D-)
GND: C7.2, C8.1, C9.2, C10.2, C11.2, C12.2, C13.2, C14.2, C15.2, C16.2, C17.2, C18.2, C19.2, C20.2, C21.2, C22.2, C23.2, D5.1 (K), D6.1 (K), J9.5 (GND), J9.6 (Shield), R17.2, R18.1, R19.1, RV1.2, RV2.2, SW1.2, U3.5 (UGND), U3.15 (GND), U3.23 (GND), U3.35 (GND), U3.43 (GND), U4.1 (GND), U5.2 (GND); also elsewhere on the board
unnamed: C7.1, U3.17 (XTAL1), Y1.2
unnamed: C8.2, U3.16 (XTAL2), Y1.1
unnamed: C9.1, U3.42 (AREF)
unnamed: C10.1, U3.6 (UCAP)
unnamed: C16.1, C17.1, Q4.2 (S), U4.3 (VI)
unnamed: C20.1, F1.1, J9.1 (VBUS)
unnamed: D5.2 (A), R15.2
unnamed: D6.2 (A), R16.2
unnamed: J9.2 (D-), R21.2, RV1.1
unnamed: J9.3 (D+), R20.1, RV2.1
unnamed: R15.1, U3.8 (PB0)
unnamed: R16.1, U3.22 (PD5)
unnamed: R17.1, U3.33 (~HWB~/PE2)
RESET: D4.2 (A), R14.1, SW1.1, U3.13 (~RESET); also elsewhere on the board
VBUS: C15.1, F1.2, Q3.3 (D), R19.2, U3.7 (VBUS)
VDD: Q3.1 (G), Q4.3 (D), R18.2; also elsewhere on the board

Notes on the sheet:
Microcontroller
USB Interface
Power Management and Selection

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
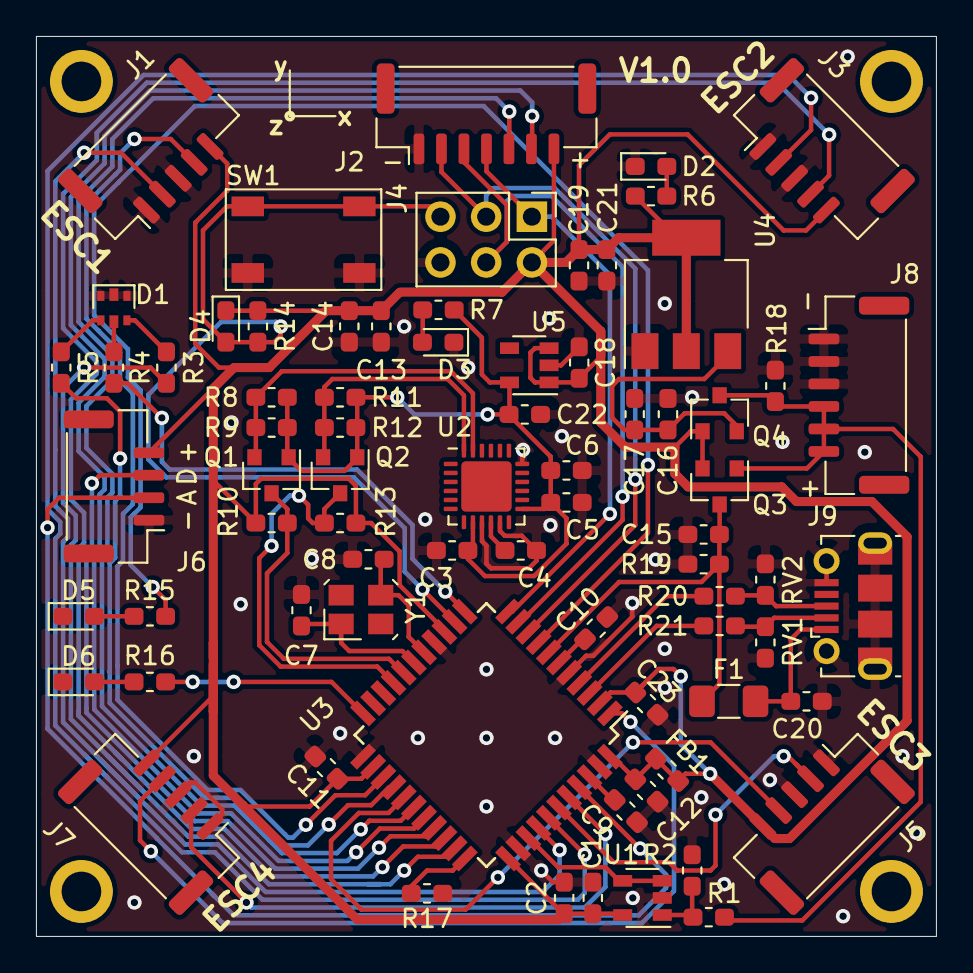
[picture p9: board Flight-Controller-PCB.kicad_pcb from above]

Board: 2 copper layers, 50.0 x 50.0 mm, 78 parts (0 on the bottom side), 51 nets.

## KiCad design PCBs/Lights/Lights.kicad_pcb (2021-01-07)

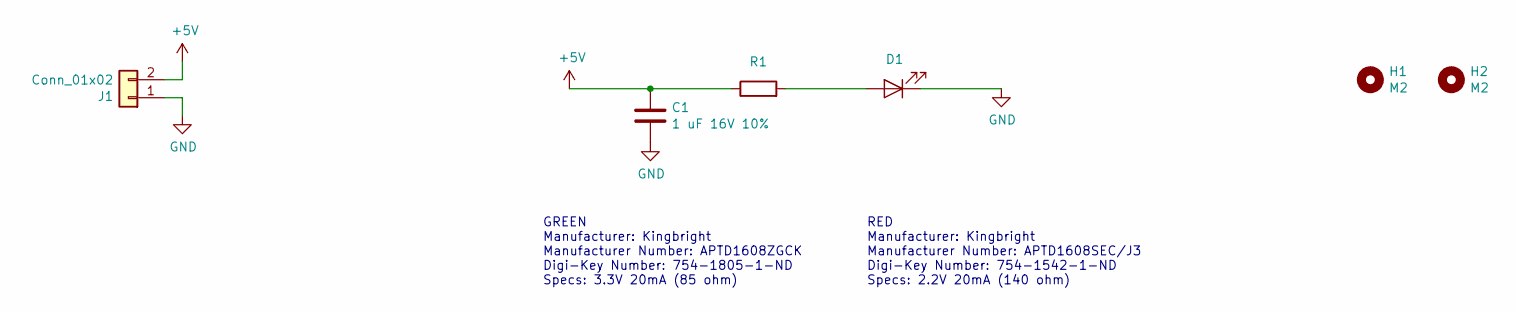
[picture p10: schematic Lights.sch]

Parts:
C1: 1 uF 16V 10%; C_0603_1608Metric_Pad1.05x0.95mm_HandSolder
D1: See Notes; LED_0603_1608Metric_Pad1.05x0.95mm_HandSolder
H1, H2: M2; MountingHole_2.2mm_M2_ISO14580_Pad
J1: Conn_01x02; JST_GH_SM02B-GHS-TB_1x02-1MP_P1.25mm_Horizontal; Manufacturer # SM02B-GHS-TB(LF)(SN); Digi-Key # 455-1564-1-ND
R1: See Notes; R_0603_1608Metric_Pad1.05x0.95mm_HandSolder

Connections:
+5V: C1.1, J1.2, R1.1
GND: C1.2, D1.1 (K), J1.1
unnamed: D1.2 (A), R1.2

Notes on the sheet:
GREEN Manufacturer: Kingbright Manufacturer Number: APTD1608ZGCK Digi-Key Number: 754-1805-1-ND Specs: 3.3V 20mA (85 ohm)
RED Manufacturer: Kingbright Manufacturer Number: APTD1608SEC/J3 Digi-Key Number: 754-1542-1-ND Specs: 2.2V 20mA (140 ohm)

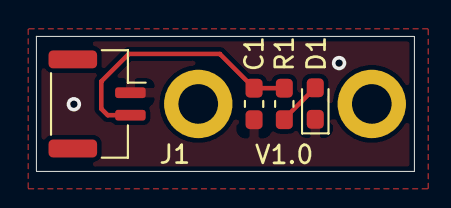
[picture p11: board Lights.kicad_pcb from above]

Board: 2 copper layers, 21.0 x 7.5 mm, 6 parts (0 on the bottom side), 3 nets.

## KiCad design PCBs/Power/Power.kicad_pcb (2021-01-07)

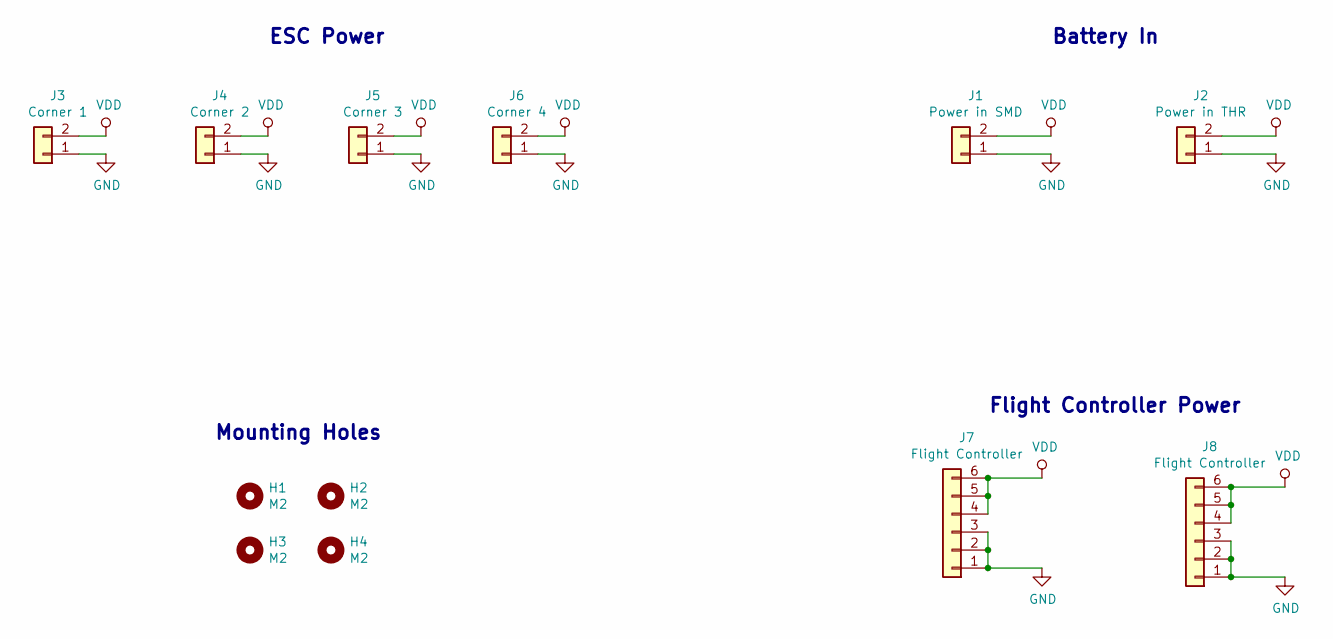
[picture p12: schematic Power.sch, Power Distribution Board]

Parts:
H1, H2, H3, H4: M2; MountingHole_2.2mm_M2_ISO14580_Pad
J1: Power in SMD; SMD-Power
J2: Power in THR; THR-Power
J3: Corner 1; Corner-Pad
J4: Corner 2; Corner-Pad
J5: Corner 3; Corner-Pad
J6: Corner 4; Corner-Pad
J7: Flight Controller; JST_GH_BM06B-GHS-TBT_1x06-1MP_P1.25mm_Vertical
J8: Flight Controller; JST_GH_SM06B-GHS-TB_1x06-1MP_P1.25mm_Horizontal

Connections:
GND: J1.1, J2.1, J3.1, J4.1, J5.1, J6.1, J7.1, J7.2, J7.3, J8.1, J8.2, J8.3
VDD: J1.2, J2.2, J3.2, J4.2, J5.2, J6.2, J7.4, J7.5, J7.6, J8.4, J8.5, J8.6

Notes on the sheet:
ESC Power
Battery In
Mounting Holes
Flight Controller Power

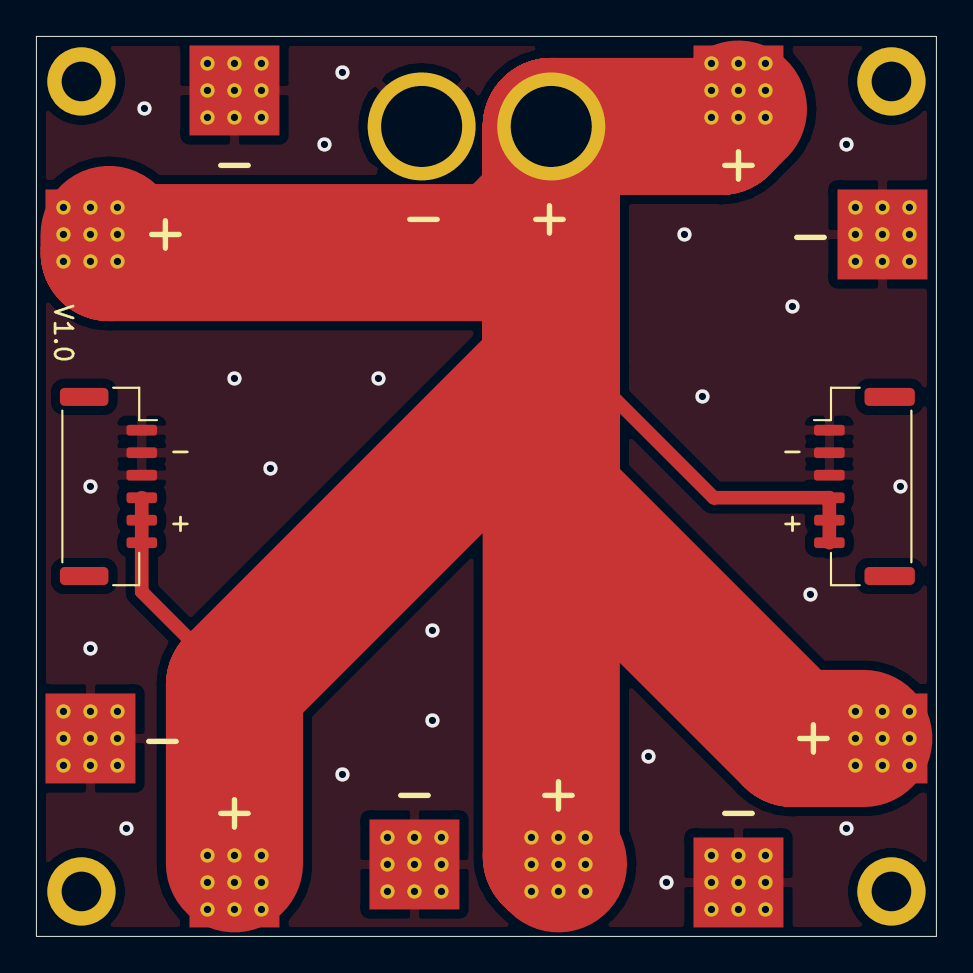
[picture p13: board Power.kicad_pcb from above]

Board: 2 copper layers, 50.0 x 50.0 mm, 12 parts (0 on the bottom side), 2 nets.

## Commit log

2020-12-13 PCB initial commit
    [Main-Board.kicad_pcb, Main-Board.sch]
2020-12-13 ICM-20689 symbol created
    [Main-Board.sch]
2020-12-14 roughed out the imu schematic
    [Main-Board.sch]
2020-12-15 Select ATMEGA328P as main processor, started to route.
    [Main-Board.sch]
2020-12-16 Gave everything their own sheet and made schematic for USB interface. USE 5 v logic for now
    [IMU.sch, Main-Board.sch, Microcontroller.sch]
2020-12-17 Added in microcontroller voltage regulation
    [Main-Board.sch, Microcontroller.sch]
2020-12-18 Roughed the rest of the microcontroller schematic
    [Main-Board.sch, Microcontroller.sch]
2020-12-19 Added battery monitoring, some RGB LED, and general org
    [IMU.sch, Main-Board.sch, Microcontroller.sch]
2020-12-19 Add RGB LED and added some additional pinout
    [Main-Board.sch]
2020-12-19 Filled out majority of microcontroller components and foot prints
    [Microcontroller.sch]
2020-12-19 Added a few more footprints and component specifics. Created first net list
    [IMU.sch, Main-Board.kicad_pcb, Main-Board.sch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]
2020-12-20 Everything is in the schematic. Just need to review board then start the layout. Printed off hard copy
    [Main-Board.kicad_pcb, Main-Board.sch, Microcontroller.sch]
2020-12-20 Checked over page one, biggest question is what connectors to use
    [Main-Board.kicad_pcb, Main-Board.sch]
2020-12-20 Change to JST-GH connectors
    [Main-Board.kicad_pcb, Main-Board.sch]
2020-12-21 Review IMU, changed power in connector to 6 pos to prevent mis mating
    [IMU.sch, Main-Board.sch, Microcontroller.sch]
2020-12-21 Initial glance over microcontroller schematic
    [Microcontroller.sch]
2020-12-21 Reviewed MCU. Next have to generate BOM and route board
    [Main-Board.kicad_pcb, Microcontroller.sch]
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2020-12-21 Minor updates for components to reflect BOM
    [IMU.sch, Main-Board.sch, Microcontroller.sch]
2020-12-21 BOM initial commit
    [Main-Board.csv, Microcontroller.sch]
2020-12-21 Switched from crystal to Resonator
    [Main-Board.csv, Main-Board.kicad_pcb, Main-Board.sch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]
2020-12-22 Routed IMU
    [Main-Board.kicad_pcb]
2020-12-22 Shrunk board to approx 65 mm and layed out approx positions
    [Main-Board.kicad_pcb, Main-Board.sch]
2020-12-22 Dimensions 50 mm x 50 mm with 45 mm c-c holes. ESC connectors placed
    [Main-Board.kicad_pcb]
2020-12-22 50% usb, ICSP, voltage monitoring, SDA/SCL, 48 tracks to go
    [Main-Board.kicad_pcb]
2020-12-22 USB and voltage regulator routed, all components are now on the board
    [Main-Board.kicad_pcb]
2020-12-22 more routing, back up before fixing some errors
    [Main-Board.kicad_pcb]
2020-12-22 add attacheted lights to open ATMEGA ports (A4 cant be used again, dont mess with tx/rx) and removed 5th rc input. Add cap for USB
    [Main-Board.kicad_pcb, Main-Board.sch, Microcontroller.sch]
2020-12-23 New schematic time... Switching to ATmega32U4
    [Flight-Controller-PCB.kicad_pcb, Flight-Controller-PCB.sch, IMU.sch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]
2020-12-23 Deleted majority of unused components. Started schematic for new MCU
    [Flight-Controller-PCB.sch, IMU.sch, Microcontroller.sch]
2020-12-24 Learned a lot about crystals
    [Microcontroller.sch]
2020-12-24 Power Management and Selection roughed out
    [Flight-Controller-PCB.kicad_pcb, IMU.sch, Microcontroller.sch]
2020-12-24 USB interface
    [Microcontroller.sch]
2020-12-30 Push before branch switch
    [Flight-Controller-PCB.sch, Microcontroller.sch]
2021-01-01 Mostly finished off the schematic, need to double check and label
    [Flight-Controller-PCB.sch, IMU.sch, Microcontroller.sch]
2021-01-01 Updated pin mappings
    [Flight-Controller-PCB.sch, IMU.sch, Microcontroller.sch]
2021-01-01 Main page and IMU reviewed and passed
    [Flight-Controller-PCB.sch, IMU.sch, Microcontroller.sch]
2021-01-01 Microcontroller reviewed
    [Microcontroller.sch]
2021-01-01 clean up refernces
    [Microcontroller.sch]
2021-01-02 Create BOM and schematic
    [BOM.csv, Flight-Controller-PCB.kicad_pcb, Microcontroller.sch]
2021-01-02 Remove V0 PCB
    [IMU.sch, Main-Board.kicad_pcb, Main-Board.sch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]
2021-01-02 Group components
    [Flight-Controller-PCB.kicad_pcb]
2021-01-02 Placed the crystal and IMU is mostly routed
    [Flight-Controller-PCB.kicad_pcb, Flight-Controller-PCB.sch, Microcontroller.sch]
2021-01-02 Power regulators routed
    [Flight-Controller-PCB.kicad_pcb, Microcontroller.sch]
2021-01-02 everything placed
    [Flight-Controller-PCB.kicad_pcb, Microcontroller.sch]
2021-01-02 Moved all components to the top of the board
    [Flight-Controller-PCB.kicad_pcb, Microcontroller.sch]
2021-01-02 35 some traces left
    [Flight-Controller-PCB.kicad_pcb]
2021-01-02 18 Traces left
    [Flight-Controller-PCB.kicad_pcb]
2021-01-03 5 unrouted
    [Flight-Controller-PCB.kicad_pcb]
2021-01-03 Silk screen and DRC then done. One Unrouted bug?'
    [Flight-Controller-PCB.kicad_pcb]
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2021-01-03 Make gerbers and PDF schematic
    [Lights-B_Cu.gbr, Lights-B_Mask.gbr, Lights-B_Paste.gbr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]
2021-01-04 Started schematic and board, created custom footprints
    [Power.kicad_pcb, Power.sch]
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2021-01-05 fix + and - silk screen error
    [Power-B_Cu.gbr, Power-B_Mask.gbr, Power-B_Paste.gbr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]
2021-01-07 Update file strcture before pull request
    [BOM.csv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]
2021-01-10 Refresh the schematic and BOM
    [BOM.csv]
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2021-01-10 Update part numbers and create BOM
    [BOM.csv, Power.sch]
